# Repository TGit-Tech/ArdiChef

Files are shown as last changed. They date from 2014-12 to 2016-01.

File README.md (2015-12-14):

-----------------------------------------------------------------------------------
#ABOUT
-----------------------------------------------------------------------------------
ArdiChef is a project that will attempt to automate home cooking
and cleaning.  The project will utilize

    - Arduino microcontroller kits
    - 3D Printed food dispensing parts
    - Purchased pumps, motors and miscellaneous hardware

ArdiChef will take a factory automation approach in dealing with
food preparation much like a in-home food factory.

-----------------------------------------------------------------------------------
#Project Status
-----------------------------------------------------------------------------------
ArdiChef is still in a development phase and has no official releases.  

RELEASE TARGET-DATES

    * 1/2016    v1.0 - Basic ingredient dispensing (ArdiChef-100 Releasing Soon)
    * 6/2016    v2.0 - Ingredient mixing & prep
    * 1/2017    v3.0 - Cooking
    * 6/2017    v4.0 - Self Cleaning abilities

-----------------------------------------------------------------------------------
CONTRIBUTING
-----------------------------------------------------------------------------------
Anyone interested in joining this project can email
tgit28@gmail.com with a return email address.  Details of what can
be done and what needs done can be negotiated from there.

We'd really appreciate any extra man-power we can gather..

CONTRIBUTORS

    Thomas G.      Project Started         tgit28@gmail.com
    
-----------------------------------------------------------------------------------
WERE TO GO FROM HERE
-----------------------------------------------------------------------------------
ArdiChef has a website at http://www.ArdiChef.com that shows more
details on what has been made and how to assemble the items finished.

Also take a look at /documents/ArdiChef_v1.0.pdf for project details.
https://github.com/tgit23/ArdiChef/blob/master/documents/ArdiChef_v1.0.pdf

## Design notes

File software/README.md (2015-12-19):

# Software
#####For the ArdiChef Project
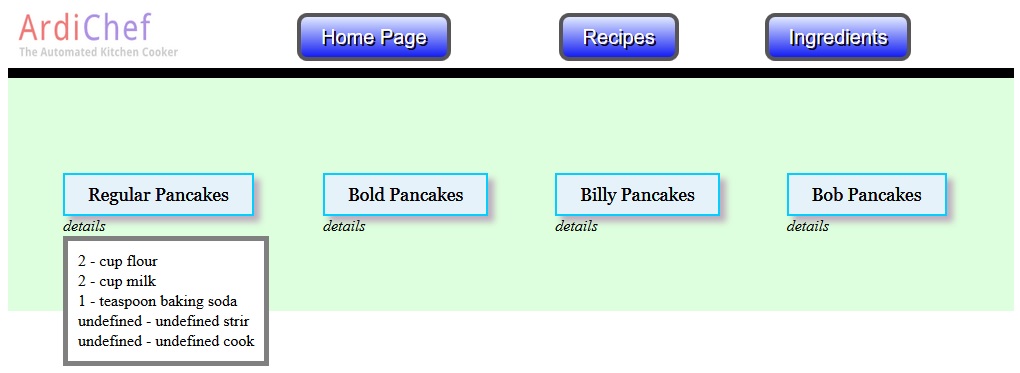
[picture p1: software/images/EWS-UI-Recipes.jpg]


-------------------------------------------------------------------------------------
##Choosing a Hardware Configuration
-------------------------------------------------------------------------------------
1. ArdiChef will support various hardware configurations to meet complexity needs
    - Single Arduino Board
    - Single Arduino Board with Ethernet Shield (*SUGGESTED*)
    - One Arduino Board and one Rasberry Pi
    - Multiple Arduino Boards with a "master" Arduino Board with an Ethernet Shield
    - Multiple Arduino Boards with one Rasberry Pi

-------------------------------------------------------------------------------------
##Software Installation ( Single Arduino with Ethernet )
-------------------------------------------------------------------------------------
1. Arduino Setup
    - Load ArdiChefController into Arduino Sketch
    - Set Pre-Compiler Directives
        - IP Adress
        - Gateway
        - Subnet
    - Compile and Upload to the Arduino
    
    - Setup the EWS
        - Copy all files within the EWS folder to the Ethernet Shield SD-Card
        - Plug the card back into the Ethernet Shield
        
-------------------------------------------------------------------------------------
##Architecture
-------------------------------------------------------------------------------------
- The main components of ArdiChef Software include
    - A **Storage** device
    - An Embedded Web Server (**EWS**) to host the files on the storage device
    - A Web **Browser** that supports Javascript for the User Interface
    - I2C or Serial **Communications** (*For Multiple Arduino Boards*)
    - **Ports** Dispatch/Pin routing and Various Motor/Heat/Other Driving objects (*Always on Arduino*)

- Single Arduino Board Configuration (*Still In Development*)
    - Storage = Recipe & Ingredient files reside locally on a USB attached home PC.
    - EWS = Files are hosted on the home PC
    - Browser = Any javascript enabled web browser on the home PC
    - Communications = USB -> |Firmata/Serial| -> Arduino
    - Ports = "ArdiChefController" Arduino Sketch

- Single Arduino Board with Ethernet Shield
    - Storage = Micro SD-Card
    - EWS = Arduino
    - Browser = Any Browser on the local network (ie. Home PC or Cell Phone)
    - Ports = "ArdiChefController" Arduino Sketch

- Single Arduino and Rasberry Pi (*Still In Development*)
    - Storage = Rasberry Pi
    - EWS = Rasberry Pi
    - Browser = Rasberry Pi (*Likely equiped with a touchscreen*) and/or Any Browser on the network
    - Ports = "ArdiChefController" Arduino Sketch

- Multiple Arduino Boards with a "Master" Arduino w/Ethernet (*Still In Development*)
    - Storage = Micro SD-Card on Ethernet Shield
    - EWS = "Master" Arduino Board
    - Browser = Home PC or Cell on the network
    - Ports = "ArdiChefController" Arduino Sketch loaded on every Arduino Board Used
    
-------------------------------------------------------------------------------------
#Folders
-------------------------------------------------------------------------------------
| Folder | Contents |
| --- | ---|
| /ArdiChefController | Main Control software for Arduino Board(s) |
| /EWS (Embedded Web Server) | The files that make up the web based user interface |
| /WebServerST_Plus | Arduino Sketch for the Arduino Ethernet shield enabling EWS hosting |

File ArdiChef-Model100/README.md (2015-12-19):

#Building the ArdiChef
### Model-100
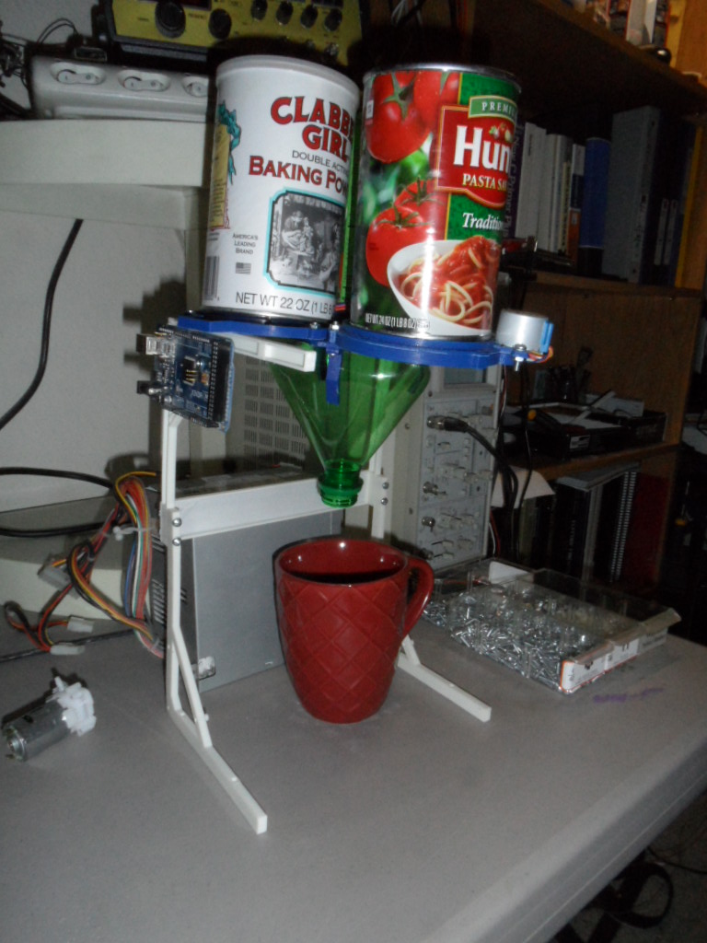
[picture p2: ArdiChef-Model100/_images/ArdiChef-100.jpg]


-------------------------------------------------------------------------------------
#Overview
-------------------------------------------------------------------------------------
- Features
    - (3) Dry Powder or Granular Ingredient Dispensing
    - Stand
        - Built from 3D Printed Parts
        - Dimensions: 11-1/4" Heigh x 8" Wide x 10-1/2"
        - 6-1/2" Nozzle Clearance
        - Mounting holes for Arduino Mega

- Example Uses
    - Simple Pancake batter w/o Eggs
    - Coffee Subliment dispensing

-------------------------------------------------------------------------------------
#Required Materials
-------------------------------------------------------------------------------------
- Household Items ~$7
    - (3) 86mm Diameter Tin Cans (ie. *Canisters*)
        - Example Items:
            - Hunts Pasta Sauce
            - Cambells Family Size Soup Cans
    - (1) 2-Liter Coca-Cola Brand Plastic Pop Bottle
        - Example Items:
            - 2-Liter Barq Root Beer
            - 2-Liter Sprite
            - 2-Liter Coca-Cola

- 3D Printed Items
    - (3) Food Dispensers (*ArdiChef Part ID: PD-FBD-28BYJ-86MM*)
    - (4) Stand Legs
    - (3) Funnel Brackets for 2-Liter pop bottle
    - Center Clamp
    - Stand Cross Member

- Electronic Hardware ~$44.10
    - Arduino AtMega 2560 Controller Board
        - <a href="http://www.gearbest.com/development-boards/pp_18651.html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" target="_blank">Arduino Mega $10.75</a>
    - Arduino Ethernet Shield with SD-Card support
        - <a href="http://www.banggood.com/Ethernet-Shield-W5100-Mega2560-R3-ATmega2560-16AU-Kit-For-Arduino-p-957681.html" target="_blank">Arduino Mega w/Ethernet Shield $17.00</a>
    - SD-Card with ability to transfer files
        - <a href="http://www.banggood.com/8GB-Class-10-Micro-SD-Card-TF-Card-With-Card-Adapter-For-Cellphone-p-1009135.html" target="_blank">8GB Class 10 Micro SD with Adapter $6.29</a>
    - Ethernet Cable
        - <a href="http://www.gearbest.com/cables-connectors/pp_68121.html" target="_blank">Retractable Ethernet Cable $1.40</a>
    - (3) 2BYJ-48 5Vdc Step Motor with ULN2003 driver board
        - <a href="http://www.gearbest.com/development-boards/pp_45177.html" target="_blank">28BYJ w/ULN2003 $3.47</a>
    - PC Power Supply
        - <a href="https://www.allhdd.com/power-supply/desktop-power-supply/250-watt/nps-250kb-f-dell-250-watt-power-supply-for-optiplex.-new-pull./" target="_blank">Dell 250W Power Supply Used $9</a>

- Mechanical Hardware
    - Machine Screws
    - Can Opener
    - Screw driver and Socket or Anything to hold the nut

-----------------------------------------------------------------------------------
##Assembly
-----------------------------------------------------------------------------------
1. Prepare (3) PD-FBD-28BYJ-83MM Food Dispensers
    - Build Instructions at: [../dispensers/PD-PowderDispensers/PD-FBD-28BYJ-86MM/README.md](../dispensers/PD-PowderDispensers/PD-FBD-28BYJ-86MM/README.md)
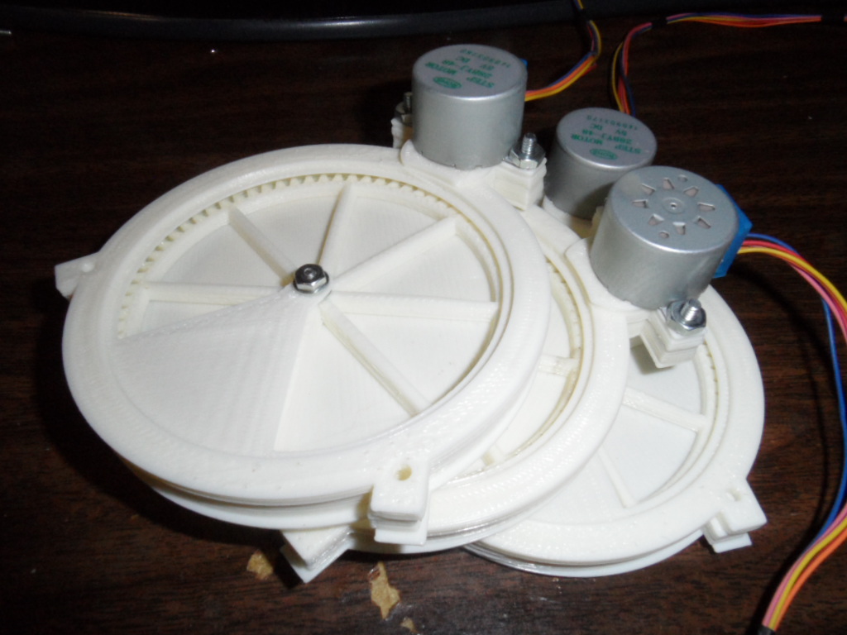
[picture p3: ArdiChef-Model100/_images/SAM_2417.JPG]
    
    
2. Attach the Dispensers together into a Triangular Collection
    - Insert #4 Machine Screws upwards in all three dispensor's side fastener holes
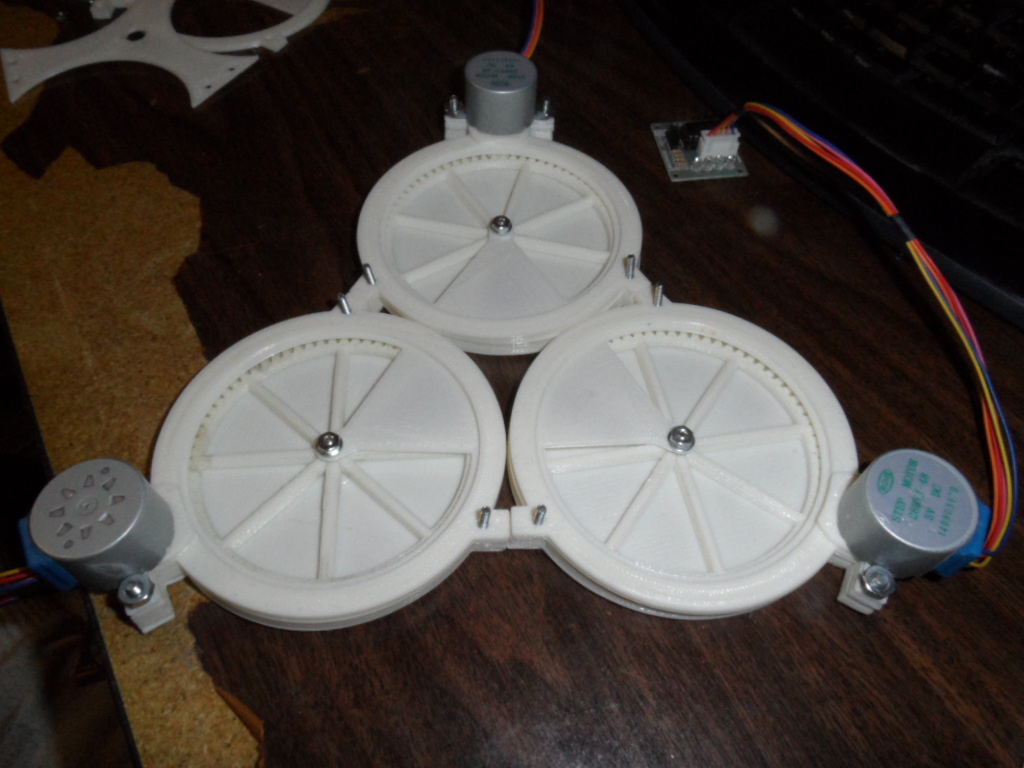
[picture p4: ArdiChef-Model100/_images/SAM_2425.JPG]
    
    - Using a can opener remove both ends of the selected cans
    - Place the cans on top of the (3) dispensers
    - Place the "Center Clamp" in the center of all 3-canisters
    
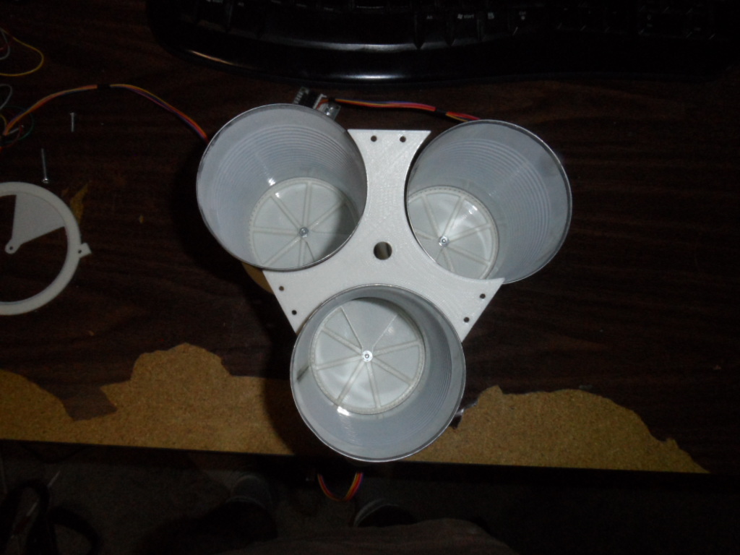
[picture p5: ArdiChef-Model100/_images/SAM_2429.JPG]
    
    - Tighten the "Center Clamp" using (6) #4 Nuts
    
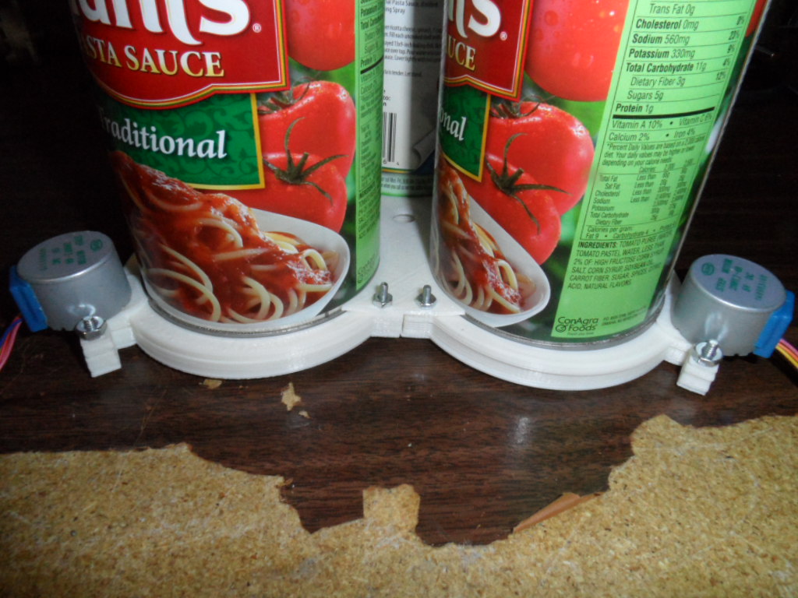
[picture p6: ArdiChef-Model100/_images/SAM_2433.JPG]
    
    - Note: *Sometimes its easier to bolt in one can at a time as long as the result is the same*
    
3. Attach the Stand
    - Using two adjacent motor bolt holes attach the stand legs to the dispenser collection
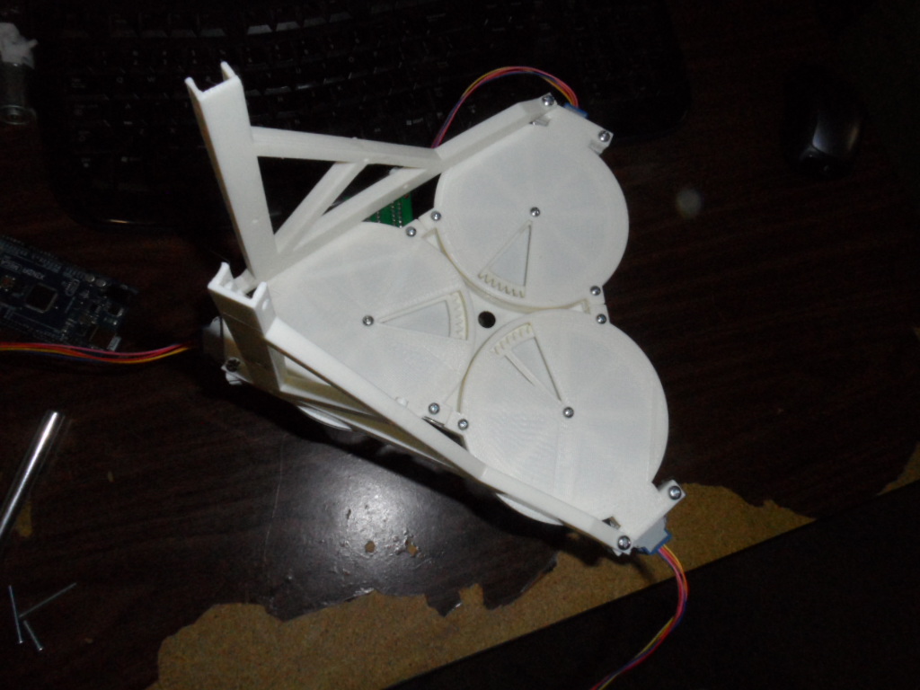
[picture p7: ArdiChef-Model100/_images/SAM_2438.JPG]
    
    
3. Attach the 2-Liter bottle as a hopper
    - Cut the 2-Liter bottle in half where the top part of it's label is
    -

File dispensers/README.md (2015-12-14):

# Food Dispensers for the ArdiChef Project
-------------------------------------------------------------------
#Labelling
-------------------------------------------------------------------
- Food Dispensers are labelled using the form 'Type'-'Model'-'Motor'-'MaxSize'-'Revision'
    - Types
        - PD = Suitable for Powder Foods Dispensing
        - GD = Suitable for Granular Foods Dispensing
    - Model
        - FBD = Full Bottom Drop
        - TDS = Top Down Scrape
    
    - Motor = Stepper Motor Model#
    - MaxSize = The largest Canister Diameter for this design
    - Revision = Optionally supply a Revision of the design

-------------------------------------------------------------------
#Examples
-------------------------------------------------------------------
- Part: PD-FBD-28BYJ-86MM
    - Powder Food Dispenser
    - Full Bottom Drop Model
    - Using 28BYJ Step Motor
    - Model Fits up to a 86mm Maximum Canister Diameter
    - No Revision version supplied

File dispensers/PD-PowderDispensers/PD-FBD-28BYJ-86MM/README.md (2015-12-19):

# Assembly Instructions
### For Part: PD-FBD-28BYJ-86MM
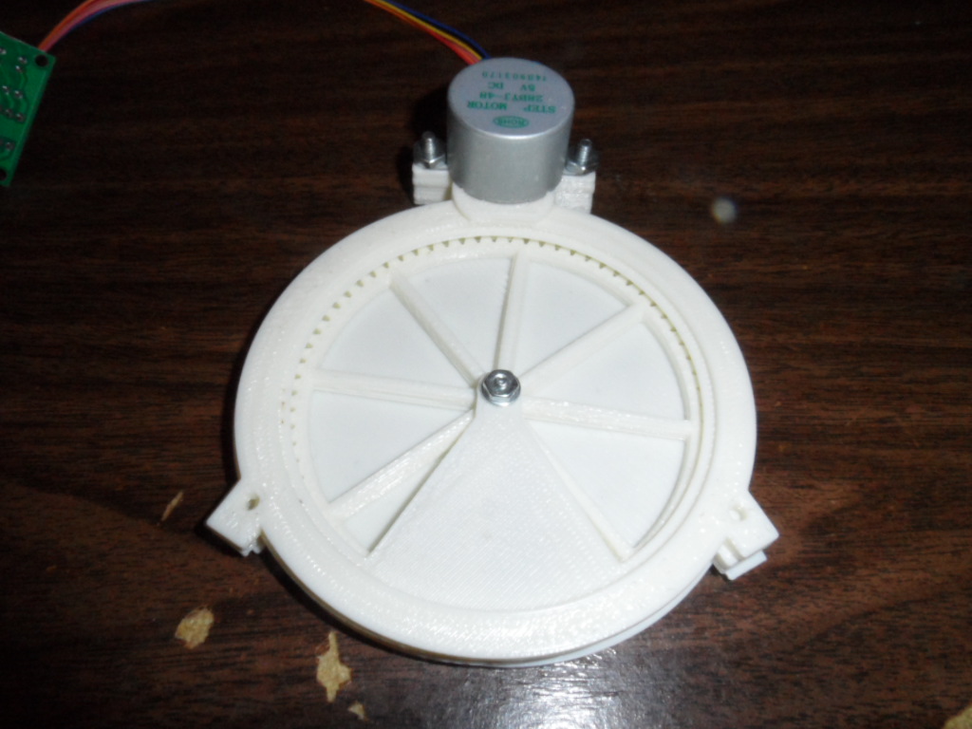
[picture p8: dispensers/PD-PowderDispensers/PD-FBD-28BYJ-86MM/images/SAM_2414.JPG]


-----------------------------------------------------------------------------------
## Bill Of Materials
-----------------------------------------------------------------------------------
1. 3D Printed Parts
    - Canister Cover
    
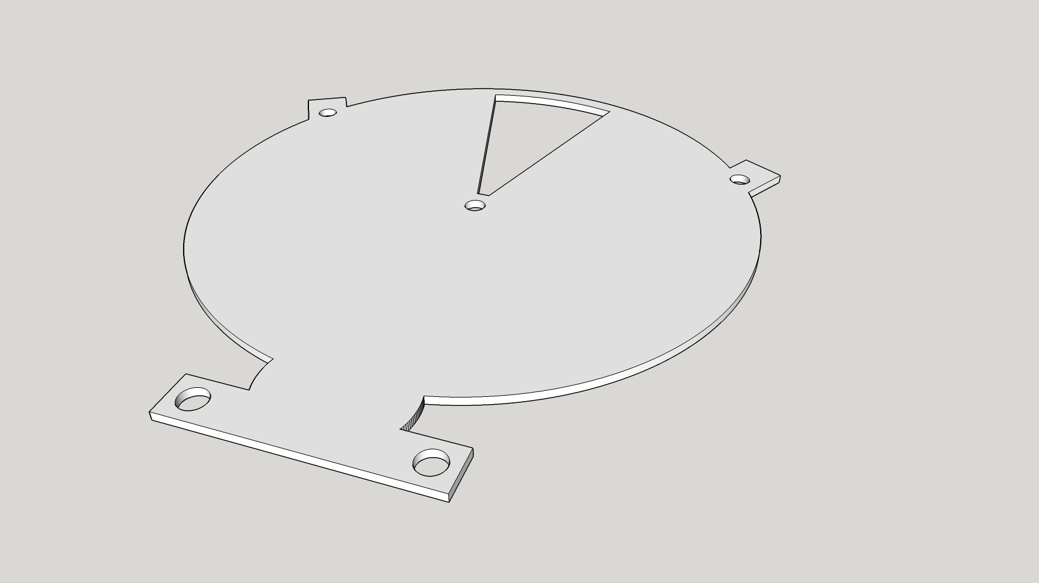
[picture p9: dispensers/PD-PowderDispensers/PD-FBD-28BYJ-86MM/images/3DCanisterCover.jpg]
    
    - Center Ring
    
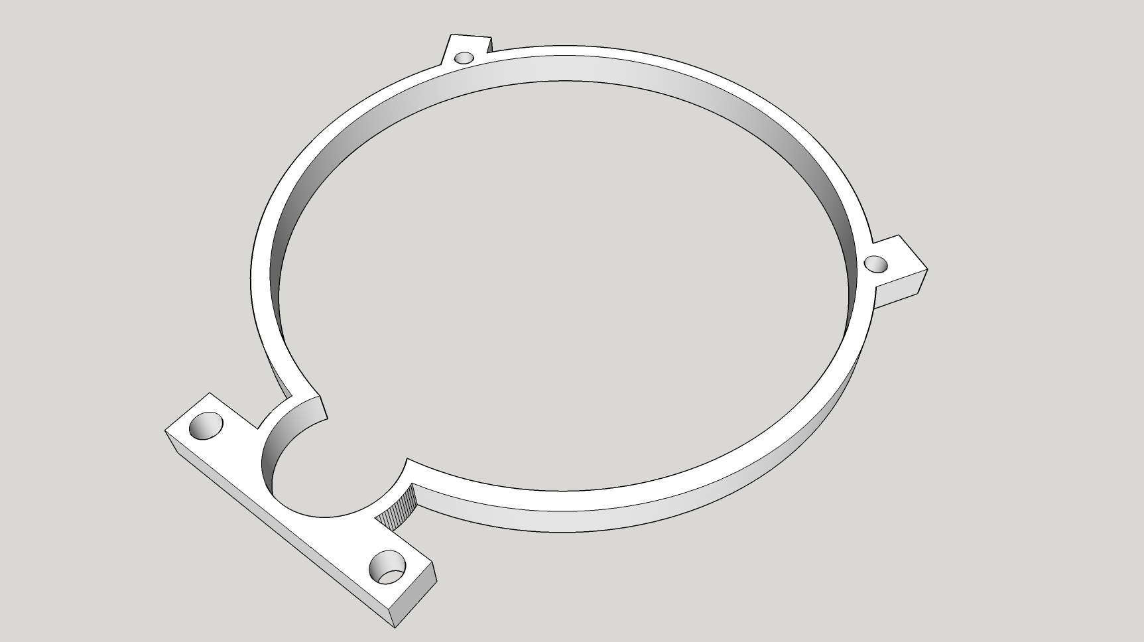
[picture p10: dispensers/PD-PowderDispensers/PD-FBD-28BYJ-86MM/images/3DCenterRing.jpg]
    
    - Dispense Gear
    
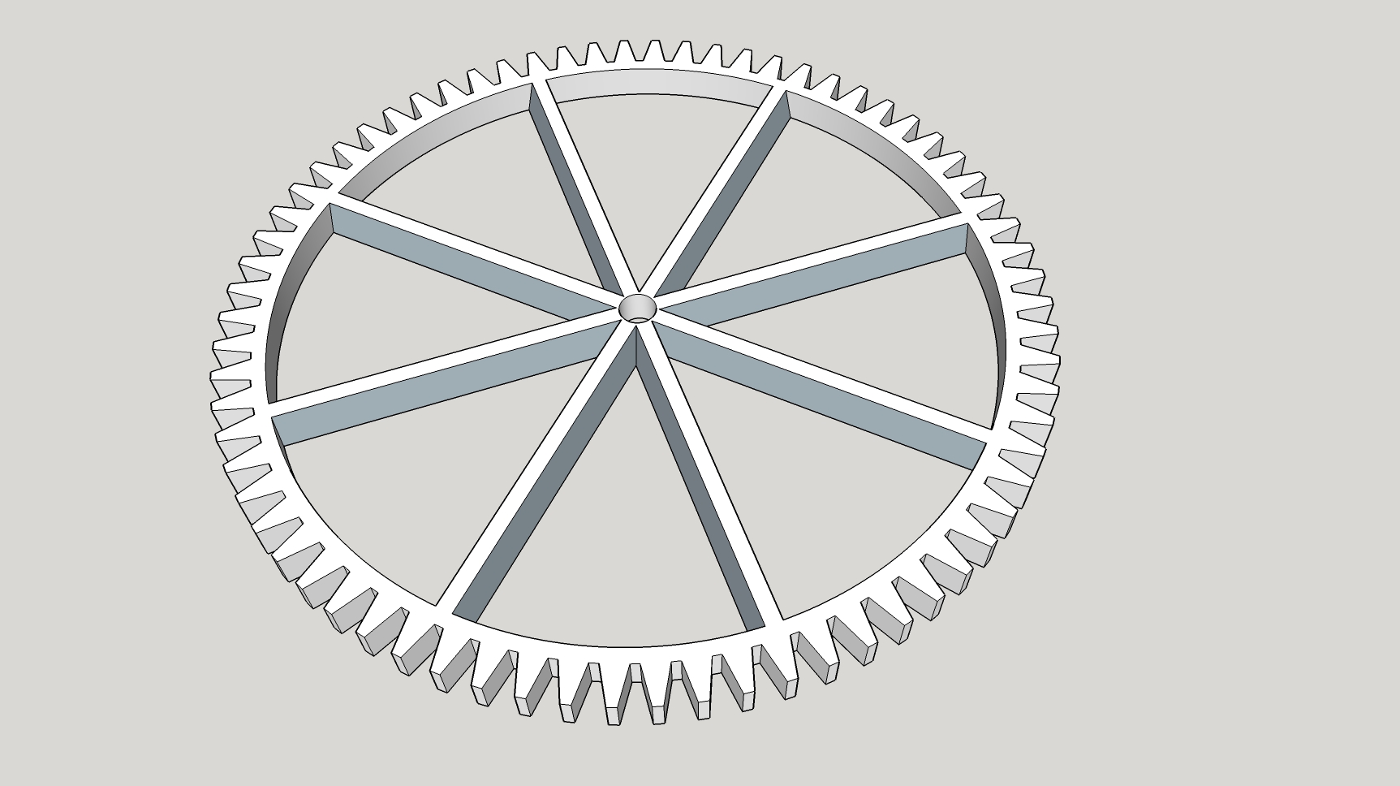
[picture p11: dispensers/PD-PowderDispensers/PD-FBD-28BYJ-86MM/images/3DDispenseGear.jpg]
    
    - Motor Gear
    
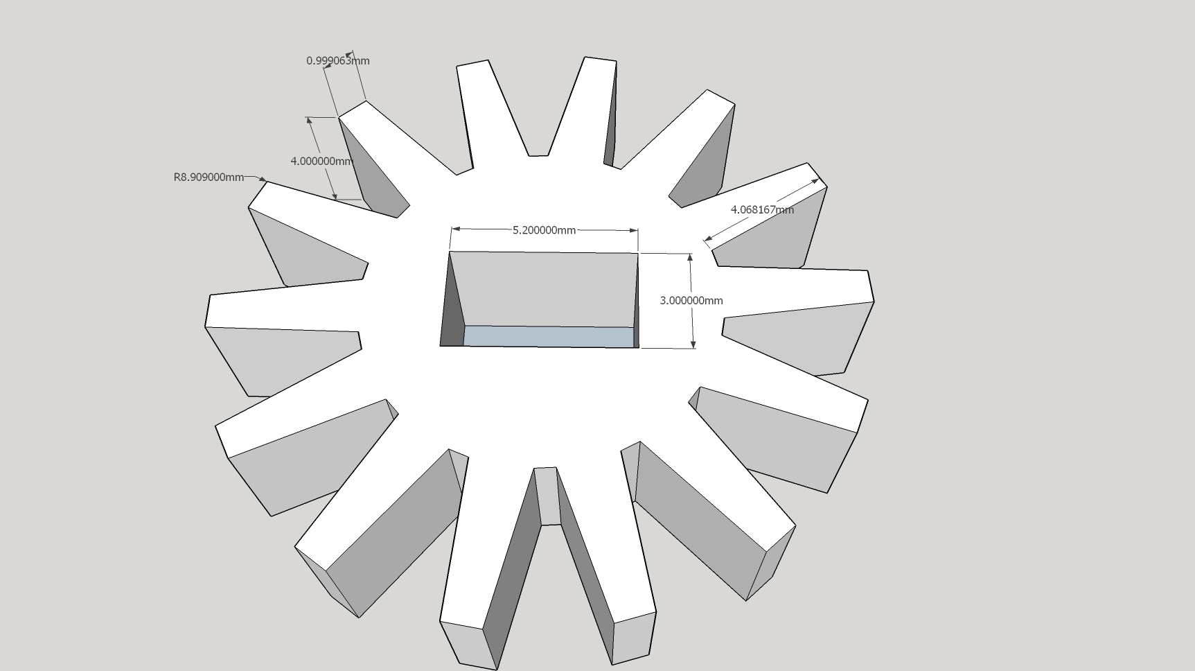
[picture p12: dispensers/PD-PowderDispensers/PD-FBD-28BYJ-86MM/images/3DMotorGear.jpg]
    
    - Canister Base
    
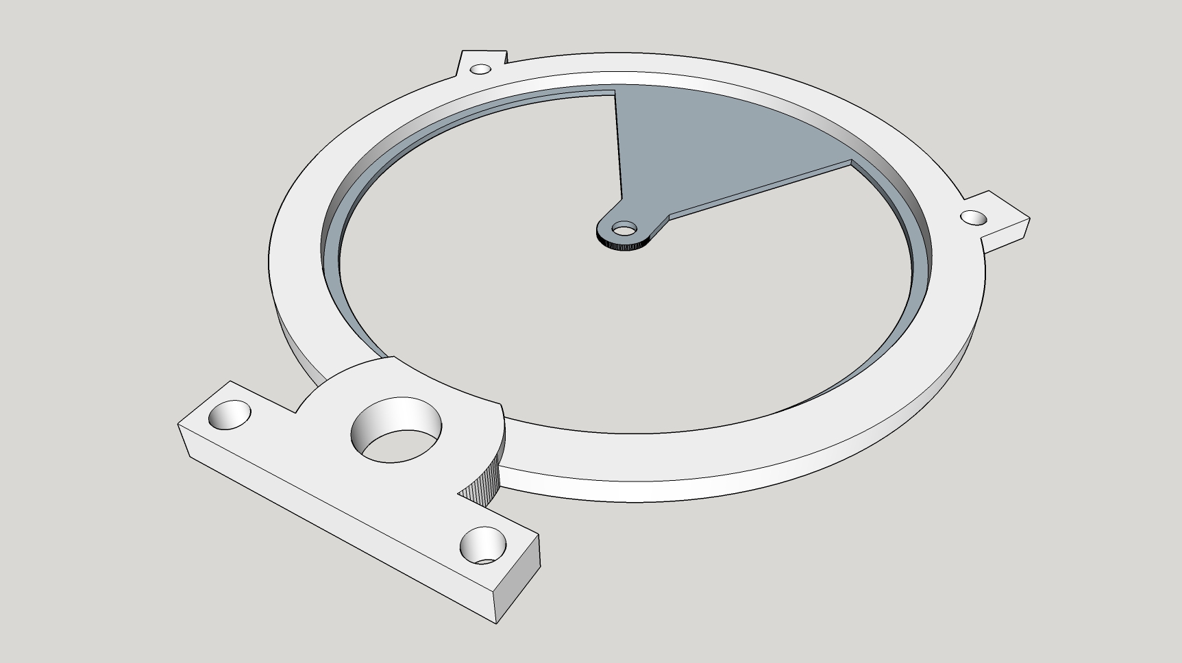
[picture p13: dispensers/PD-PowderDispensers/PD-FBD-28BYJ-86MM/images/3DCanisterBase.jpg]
    
    
2. Hardware
    - (3) #4 x 3/4" Machine Screws
    - (3) #4 Nuts
    - (3) #4 Flat Washers
    - (2) #6 or #8 x 3/4" Machine Screws
    - (2) #6 or #8 Nuts
    
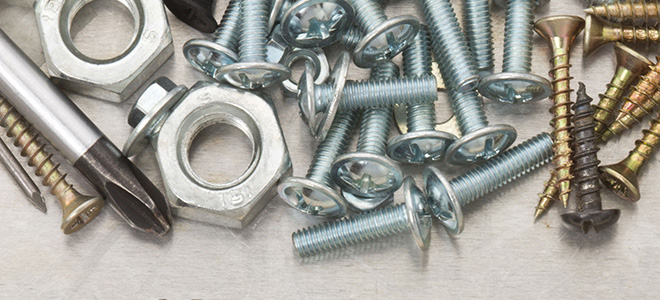
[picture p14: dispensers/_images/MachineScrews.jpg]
    
    - 28BYJ-48 Step Motor
    - ULN2003 Step Motor Driver Board
    
    
        
-----------------------------------------------------------------------------------
## Assembly
-----------------------------------------------------------------------------------
1. Place the "Canister Cover" on Work bench (smooth side up)
    - Insert a #4 x 1/2" Bolt upwards through the center
    - Place a #4 flat washer on the bolt
    - Place the "Center Ring" on top of the "Canister Cover"
    
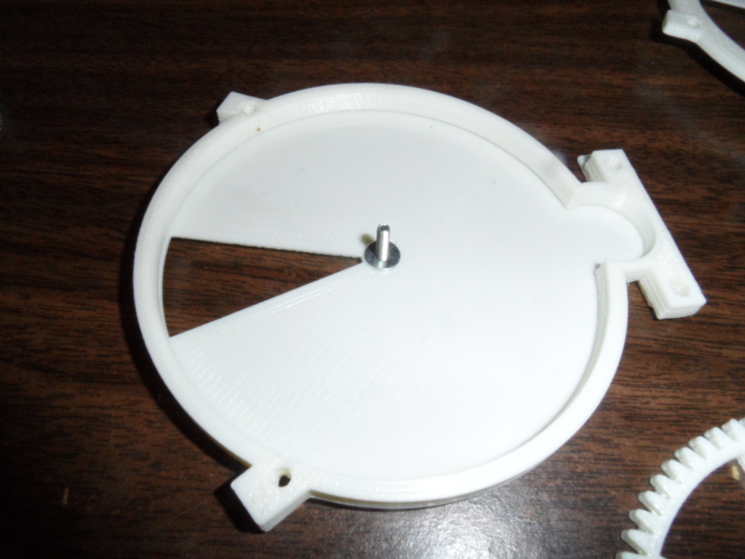
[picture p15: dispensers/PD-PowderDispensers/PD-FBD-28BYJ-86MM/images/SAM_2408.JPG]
    
    
3. Place the "Dispense Gear" inside the "Center Ring"
    - Place 2 - #4 Flat Washers on top
    
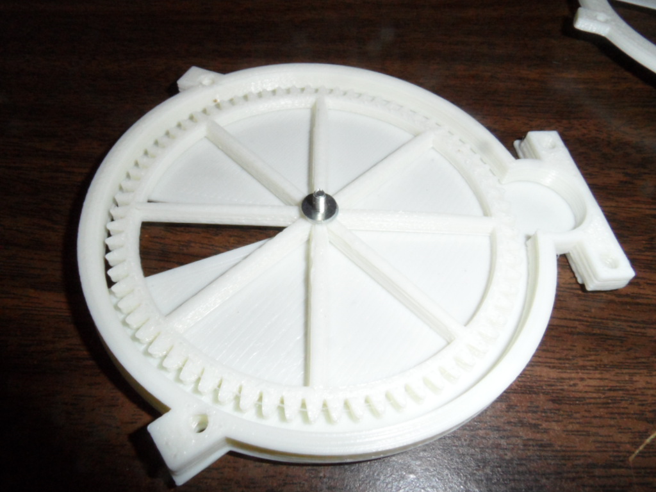
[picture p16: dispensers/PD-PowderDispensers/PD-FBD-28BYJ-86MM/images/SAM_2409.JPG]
    
    
4. Place Stepper Motor under the Canister Base (Motor meshes with the coarse side - Smooth surface up)
    - Attach the "Motor Gear" to the motor shaft (Smooth surface up)
    
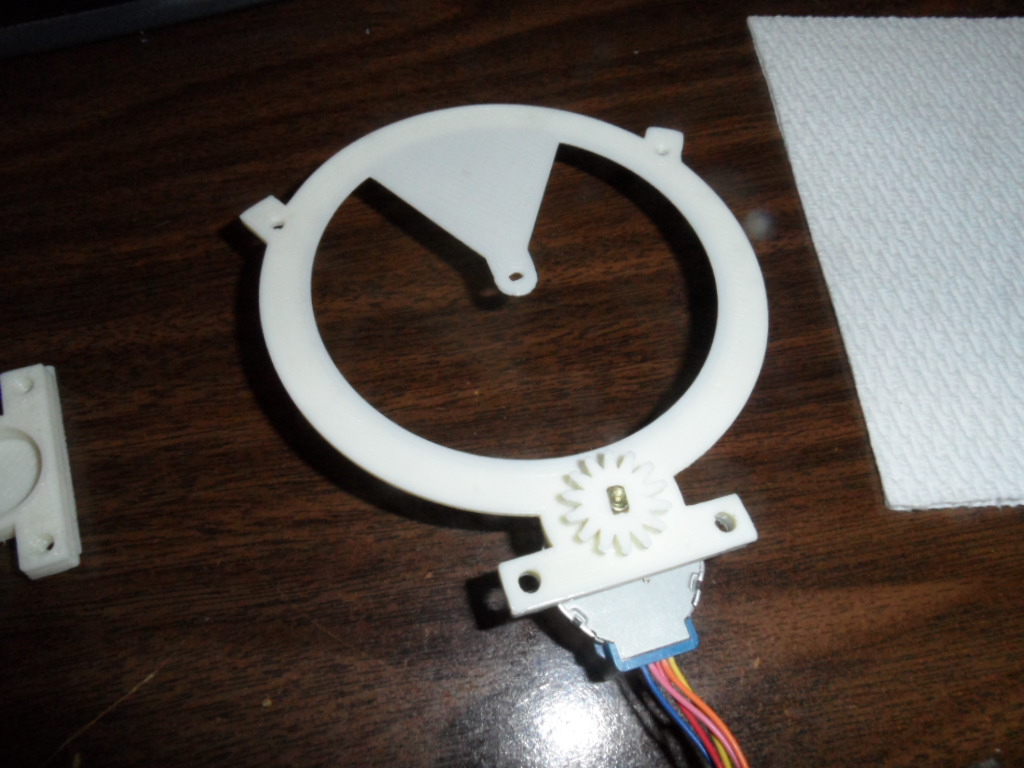
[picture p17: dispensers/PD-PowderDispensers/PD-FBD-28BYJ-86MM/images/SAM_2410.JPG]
    
    
5. Flip the "Canister Base" with Motor and place on top of the "Center Ring"
    - Attach a #4 Flat Washer on top
    
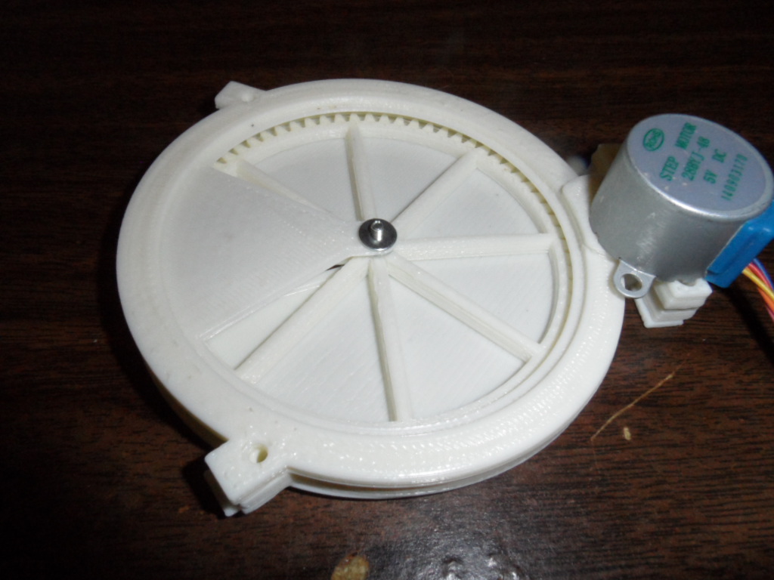
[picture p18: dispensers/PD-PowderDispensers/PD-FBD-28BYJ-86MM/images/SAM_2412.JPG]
    
    
6. Fasten the motor to the despenser
    - Use #6 x 3/4" Machine Screws
    


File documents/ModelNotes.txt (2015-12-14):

1) If "model repair service" (https://netfabb.azurewebsites.net/) keeps filling in a hole in the model
    The outer shell needs to be erased by creating the two planes (say 2mm above each other)
    Intersect face with center nut on both - fill in edges
    erase the outer edge from underneath
    
2)

------------------------------------------------------------------------------------------------------
Drawing Gears in Skethup (NONE OF THESE TRICKS WORK!!)
------------------------------------------------------------------------------------------------------
Gears in the ArdiChef Project use the attached worksheet to calculate circle radius and sides.

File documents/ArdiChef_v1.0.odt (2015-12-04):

ArdiChef Project

The Automated Kitchen Cooker

Started By: Thomas G (12/2014)

Feel free to use: no strings attached (text content only / images respectfully referenced)

# INTRODUCTION

The ArdiChef project will reside within http://www.github.com/tgit23/ArdiChef/

## Software

The software will mostly be written using the Arduino programming software package along with the "Processing" programming language.

## Control

The ArdiChef project will be controlled using the Arduino project (http://www.arduino.cc/) micro-controller board and mimic a lot of the 3D RepRap printer project technologies.

## Hardware

- Repository of Models - http://www.github.com/tgit23/Ardichef/ → Hardware/
- Bill of Materials

Many of the hardware parts are printed using a 3D printer while some will need to be purchased. Currently all 3D printed parts are designed in Google Sketchup and stored at

# FOOD DISPENSERS

## Granular Foods Dispenser (GFD-28BYJ)

Granular foods like sugars and spices can be dispensed using what I'd call the Gumball approach. A circular plate with holes in it rotating to a covered drop-hole.

### 1-Gallon Can Granular Foods Dispenser (GC-GFD-28BYJ)

The 1-Gallon granular food dispenser requires

- One Gallon Tin Can with a base diameter that measures 16.125 inches
- 28BYJ-48 5Vdc 4-Phase 5-Line Stepper Motor with ULN2003 Driver Module Board
- 3D Printer for printing the following parts @ http://www.github.com/tgit23/ArdiChef → /Hardware/GranularDispensers

File-Name | Google Sketchup | Thumb | Description
MotorMount.skp | 2014 - Inches | | 1) The 28BYJ Stepper motor is bolted into this motor mount (Shaft up)
DispGear_4inHoles.skp | 2014 -Inches | | 2) The Disp (Dispense) gear is placed on the motor shaft
GallonCanBase_6pt125inchBase.skp | 2014 - Inches | | 3) The “MotorMount/Stepper/DispGear” assembly is then bolted to the CanBase 4) The Assembly is then attached to the bottom of the One-Gallon tin can.
MotorMountSpout.skp | 2014 - Inches | | 5) Optionally – A spout holder can be attached to the MotorMount under the dispensing hole.

## Powder Foods Dispenser (PFD-28BYJ)

### 1-Gallon Can Powder Foods Dispenser (GC-PFD-28BYJ)

The 1-Gallon powder food dispenser requires

- One Gallon Tin Can with a base diameter that measures 16.125 inches
- 28BYJ-48 5Vdc 4-Phase 5-Line Stepper Motor with ULN2003 Driver Module Board
- 3/4” Shedule 80 PVC Pipe threaded and notched the height of the tin can
- 3/4” PVC Pipe Nut (Created by cutting a PVC cap)
- 3D Printer for printing the following parts located at http://www.github.com/tgit23/ArdiChef/ → Hardware/PowderDispensers/GallonCan_ThreeQtrPipe

File-Name | Build Instructions

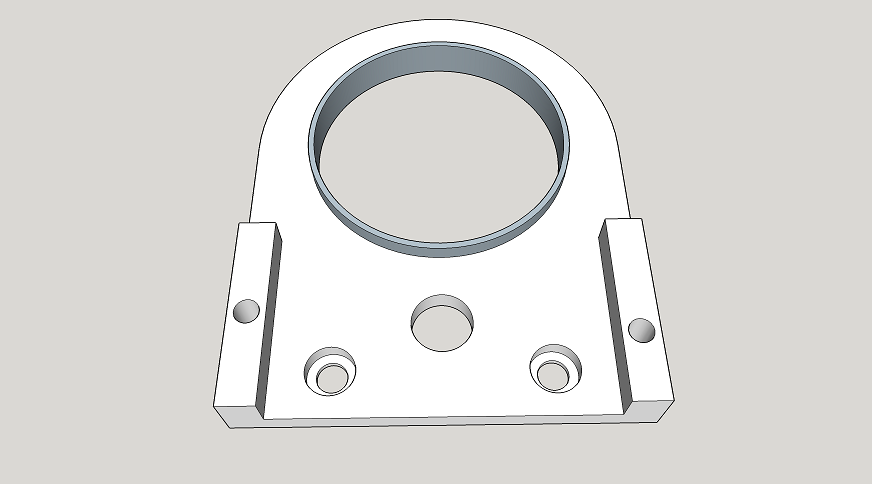
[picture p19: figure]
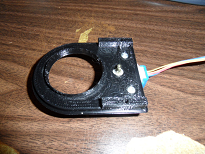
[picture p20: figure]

MotorMountGearBox.skp | 1) The 28BYJ Stepper motor is bolted into this motor mount gear box (Shaft up)
MotorGear.skp | 2) The MotorGear is placed on the motor shaft

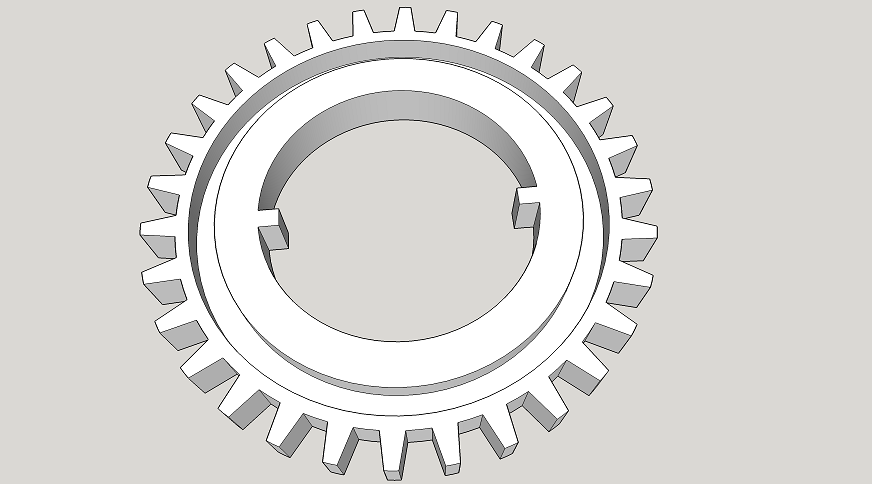
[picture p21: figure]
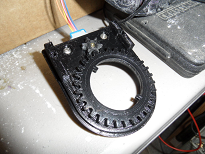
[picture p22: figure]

PipeDriverGear_24D.skp | 3) The PipeDriverGear is dropped freely into the MotorMountGearBox.

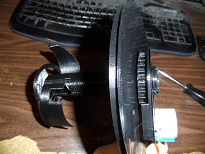
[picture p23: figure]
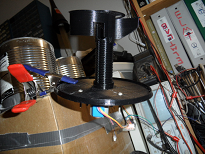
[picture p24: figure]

DispenserPipe_24D_Complete.skp CanBase_24D_1Thread.skp | 4) The MotorMountGearBox with PipeDriverGear and MotorGear Assembly is then bolted to the bottom of the CanBase. 5) The Dispensor is then Threaded Through the CanBase

### Cambells 26.25Oz Family Size Can Powder Foods Dispenser (CC-PFD-28BYJ)

The Family Size Cambells Soup Can powder food dispenser requires

- One Family Size Cambells Soup Can with a base diameter that measures 3 3/8 inches
- 28BYJ-48 5Vdc 4-Phase 5-Line Stepper Motor with ULN2003 Driver Module Board
- 1/2” Shedule 80 PVC Pipe threaded and notched the height of the tin can
- 1/2” PVC Pipe Nut (Created by cutting a PVC cap)
- 3D Printer for printing the following parts located at http://www.github.com/tgit23/ArdiChef/ → Hardware/PowderDispensers/Cambells_26.26OZ_HalfInchPipe

File-Name | Google Sketchup | Thumb | Build Instructions
MotorMountGearBox.skp | 2014 - Inches | | 1) The 28BYJ Stepper motor is bolted into this motor mount gear box (Shaft up)
MotorGear.skp | 2014 -Inches | | 2) The MotorGear is placed on the motor shaft from /PowderDispensers/GallonCan_ThreeQtrPipe
PipeDriverGear.skp | 2014 - Inches | | 3) The PipeDriverGear is dropped freely into the MotorMountGearBox.
Scrapper.skp | 2014 - Inches | | 4) A 1/2” Schedule 80 PVC pipe is threaded the height of the gallon can in use 5) Using a dremel with grinder stone create 2-notches vertically along the pipe for the DriverGear 6) The Scrapper is attached (glued) to the top of the 1/2” Threaded and notched PVC pipe.
CanBase_Campbells26.25OZ.skp | | | 7) A PVC Nut (A cut in half PVC Cap) is glued into the CanBase 8) The CanBase is then attached to the bottom of a one-gallon tin can 9) The “MotorMountGearBox/MotorGear/PipeDriverGear” assembly is bolted to the CanBase. 10) The Threaded and Notched “PVC-Pipe/Scrapper” is threaded down the CanBase Nut till the PipeDriverGear's Notches catches the Notches in the PVC pipe.

# SOFTWARE

## Architecture

SD-Card ------------------------------------------------------------------ Recipes.json Webpages.htm | Ingredients.json | I2C.json Interface Device ----------------------------- PC Tablet / Cell Phone Rasberry Pi Arduino-#0 or Rasberry Pi ------------------------------------------ WebServerST <-- |--> Master Engine ==================================== Depending on configuration Arduino #0 can host or Rasberry Pi Firmata Ethernet Motors Arduino #4 ------------------------------------------ I2C ========================== Motor Drivers Arduino ------------------ I2C =========== Motor Drivers If the Server is hosted on arduino The runtime.json is used to buffer Commands ELSE an I2C in/out Buffer on the Rasberry Pi is used.

- Hardware
  - Interface Device = Any device with a web browser
  - Arduino's = A master Arduino(#0) and any other Arduino's numbered according to their I2C address
  - Storage = SD-Card connected to Arduino #0
- Software
  - WebServerST = Renders html pages on the SD-Card, Parses AJAJ request that trigger the Master Engine
  - Master Engine = Processes requests; using Recipe.json & Ingredient.json data and outputs to → runtime.json
  - I2C communications
    - On Arduino #0 = Transmits action commands on the I2C communication bus
    - Other Arduino's = Recieves action commands
  - Drivers = Transforms “action commands” into motor activation

## Files

- Web-Pages
  - index.htm = Section (Buttons “ingredients”, “recipes”, and “manual”); Section (Buttons for all “favorite” recipes)
  - ingredients.htm = HMI type display with ingredients JSON and entries/buttons for Ingredients.json file editing
  - recipes.htm = Load, Edit, Add and Execute (IE. Send to Engine); various recipes files

### Index (json/htm)

- Top Section will have 3-Buttons to access other htm pages; “Recipes”, “Ingredients”, and “Manual” (i.e. for manual control)
- Bottom Scroll-able Section will have dynamic instantly run recipe buttons part of a category known as “favorite” recipes
  - Favorite recipe names will be stored in index.json and have a “Remove” and “Portion Size” button/fields.

### Ingredients (json/htm)

#### Ingredients.htm

- HMI graphical view of Canisters, Cooking and stuff that make up the ArdiChef.
  - Canisters should graphically show their current product level and at the top show their total capacity.
  - Each information field should be editable by clicking on it
  - Also include an “Add” button to add new Ingredient/Operation

FLOUR SUGAR

------------- ======

------------- ======

motor motor

driver driver

pulze-oz pulse-oz

manual pin manual pin

#### Ingredients.json

  - Top object ID = Arduino # (IE. 0 for master or I2C address #)
  - Digital Pins = The digital pins used by a dispenser/operation (e.g. 1-4 or 1,5,8 or etc...)
  - Ingredient = A text name for product or operation
  - Driver = The driver module name to use for motor activation; Different drivers will require more/dynamic settings
    - 28BYJ

### Recipes (json/htm)

- Recipes.htm
  - Loads recipes.json behind the scenes (AJAJ) and display as many recipe-blocks as possible; Each block having
    - Name = Recipe Name
    - “Portion” = Serving Size
    - “Edit” = Open 'this' recipe in “Recipe.htm” for editing and/or removal
    - “Favorite” = Add Recipe name to 'index.json' to display it on the home page
  - “Add” button to allow adding new recipes
  - Recipes.htm will contain javascript to organize, sort, and find recipes
- Recipes.json - All JSON Recipes will initially be one file (may break apart later as project matures)
    - “Run” button – to execute the recipe
    - “Portion” field – to proportionate the recipe
    - “Favorite” button – to add the recipe to “favorites” on the home page
    - “Edit” button – to load a new 'htm' page that will
- RecipeEdit
  - May be implemented as a pop-over screen on the same web-page (this would be the ideal way to handle it, I think.)

## Implementation

- WebServerST
  - Must contain the ability to:
    - Serve GET files - for HTML page requests
    - Serve AJAJ files - for AJAJ page data
    - POST - Ability to trigger events(ie. functions) on the Master Engine
- Master Engine
  - Steps
    - Stream through recipes.json and find the recipe to operate on
    - Calculate the portion size
    - Stream through ingredients.json to decode the recipe to driver signals (recipe → I2C.json)
    - Build the I2C.json (i.e. driver messages) file and save it in the /I2Cstack so drivers can pick it up and execute
- I2C
  - I2C will communicate to Motor Driving Code in the form of “<PinsCSV>:Driver:Steps<\n>”
    - Thus each command will identify the motor pins, # of steps, and Driver board
- Drivers
  - Reads in commands from the I2Cstack and executes them (i.e. produces motor signals)

## Future Plans

- ArdiChef.com itegration
  - Add ability send current inventory and suggest recipes to/fro Ardichef.com
  - Add ability to share your recipes with everyone
    - Perhaps tap into an existing: food.com, myfridgefood.com, and etc...?
  - Web Server
    - Arduino -or- Rasberry Pi 2 Model B will be utilized as the Web-Host Server
    - The host will store
      - Recipes XML = Organize at least 3-hierarchy levels to contain a cooking reciepe
      - Hardware Setup XML = Which pins are connected to which dispensor models and ingredient contained there-in
      - Track Amount of Ingredients XML = Amount left inside the canister??? (May skip this for now)
    - Host Pages
      - Recipe (An “add”/”run” button on recipe browser)
        - Category - Breads
        - Name - Pancakes
        - Attribute - Blueberry (May be nice for fine adjustment or personality adjustments: Like: Drink->Coffee->MyName)
          - Ingredient Amount (Cup, Oz, Lb, etc...)
          - Ingredient Name (Flour, Sugar, etc..)
  - Web browser
    - The web browser will allow
      - Ability to upload recipes

# Up For Discussion

1. 4- Canisters into one spout or 4-spouts together
2. Turn-table or Conveyor Belt
  1. Turn-Table = Rotate bowl on circular table or rotate ingredients on circular table
  2. Conveyor Belt = Use bicycle tube as a food conveyor belt from start of ingredient canister row to an end drop position
3. Mixer on mixing bowl or over-head?

# Bill Of Materials (BOM)

## Tools

- 3D Printer

## Materials

## Original Purchases

Qty/SKU/Price | Product Name / Description | Picture

(2)

106842801

$30.54

www.gearbest.com

GZGW09 3D Printer Reprap Stepper Motor Driver Module Works with Official Arduino (http://www.gearbest.com/development-boards/pp_101725.html)

GZGW09 3D Printer Reprap Stepper Motor Driver Module

Step angle: 1.8 degree
Rated voltage: DC 4.83V
Rated current: 0.84A
Phase impedance: 5.75 Ohm + / - 10 degree centigrade
Phase inductance: 9.3 mH + / - 20 degree centigrade (1kHz 1V RMA)

Holding torque: 0.48 Nm
Shaft diameter: 5mm / 0.188
Shaft length: 20mm
Motor height: 34mm
Number of lead wire: 4 wires

Product Weight: 0.22 kg
Package Weight: 0.23 kg
Product Size(L x W x H): 5.8 x 4.2 x 4.2 cm / 2.28 x 1.65 x 1.65 inches
Package Size(L x W x H): 8.0 x 6.0 x 5.0 cm

http://www.gearbest.com/development-boards/pp_101725.html

http://www.dx.com/p/gzgw09-3d-printer-4-wire-stepper-motor-silver-black-222200#.Vk0qpuKaUQk


(3) NZ0019501 $11.22 www.gearbest.com | 28BYJ-48 5V 4-Phase 5-Line Stepper Motor with ULN2003 Driver Module Board (http://www.gearbest.com/development-boards/pp_45177.html) Google Sketchup 3" x 5 3/16" Rectangular Drive Hole
(2) NZ0049801 $75.24 www.gearbest.com | Arduino MEGA2560 RepRap Circuit Sets for 3D Printer Ramps (http://www.gearbest.com/development-boards/pp_64758.html) Package Contents: 1 x MEGA2560 Circuit Sets 1 x Ramps 1.4 4 x A4988 1 x USB Cable


(1) 277147 (http://www.dx.com/p/277147) $4.99 www.dx.com | Double Tip 21cm Dupont Cable - Black + Multicolored (70 PCS) (http://www.dx.com/p/277147) | (http://www.dx.com/p/277147)


(1) 145357 (http://www.dx.com/p/145357) $7.91 www.dx.com | 3-Pin Power Adapter Socket with Rock Switch for DIY Project - Black + Red (5-Piece Pack) (http://www.dx.com/p/145357) | (http://www.dx.com/p/145357)


(1) 344826 (http://www.dx.com/p/344826) $4.80 www.dx.com | S401 1/4" Water Flow Sensor for Dispenser / Coffee Machine - White (http://www.dx.com/p/344826) | (http://www.dx.com/p/344826)


(1) 263660 (http://www.dx.com/p/263660) $10.99 www.dx.com | DIY Copper Breadboard DuPont Connection / Test Cables - Multicolored (200 PCS) (http://www.dx.com/p/263660) | (http://www.dx.com/p/263660)


(1) 123648 (http://www.dx.com/p/123648) $1.46 www.dx.com | 2.54mm Mini Jumper Connector - Black (50-Piece Pack) (http://www.dx.com/p/123648) | (http://www.dx.com/p/123648)


(1) 162180 (http://www.dx.com/p/162180) $3.91 www.dx.com | 1-Pin Female to Female DuPont Cables for Arduino (2 x 40 PCS / 21cm) (http://www.dx.com/p/162180) | (http://www.dx.com/p/162180)
(1) 206265 (http://www.dx.com/p/206265) $1.77 www.dx.com | SZF303 Small Water Pump Motor Water / Oxygen Pipe / Tube - Transparent (100cm) (http://www.dx.com/p/206265) Model SZF303 Quantity 1 Color Transparent Material Plastic housing Features Use for small fish tank oxygen supply; DIY project Specification Inner diameter: 0.2cm; Thickness: 0.4cm; Length: 100cm Application Small water pump pipe / tube English Manual/Spec No Packing List 1 x Water pipe Dimensions: 39.37 in x 0.16 in x 0.16 in (100.0 cm x 0.4 cm x 0.4 cm) Weight: 0.32 oz (9 g) | (http://www.dx.com/p/206265)


(1) 232242 (http://www.dx.com/p/232242) $2.41 www.dx.com | DIY Plastic Water Pump Line Tube - White (4 PCS) (http://www.dx.com/p/232242) Brand N/A Quantity 4 Piece(s)/pack Color White Material Plastic Compatible Models Small water pump Application Used to connect small water pump Other Feature Outer diameter: 4mm; Inner diameter: 3mm Packing List 4 x Water pump line tubes Dimensions: 1.14 in x 0.71 in x 0.16 in (2.9 cm x 1.8 cm x 0.4 cm) Weight: 0.18 oz (5 g)


(1) 203330 (http://www.dx.com/p/203330) $4.99 www.dx.com | 20904 Silicone Tube Pipe - Translucent White (5 Meters) (http://www.dx.com/p/203330) Model 20904 Quantity 1 Color Translucent white Material Silicone Specification Outer diameter: 5mm; Inner diameter: 3mm; Thickness: 12mm; Working temperature range: -65'C~200'C Features Silicone tube Application Widely used for water dispenser, coffeemaker, electronic instrument, medical equipment, wine connection tube etc. English Manual/Spec No Packing List 1 x Silicone tube (5 meters) Dimensions: 196.85 in x 0.20 in x 0.20 in (500.0 cm x 0.5 cm x 0.5 cm) Weight: 2.82 oz (80 g) | (http://www.dx.com/p/203330)


(2) 236808 (http://www.dx.com/p/236808) $5.23 www.dx.com | HSYY01 Micro Gear Water Pump Motor w/ Hose - White + Silver (http://www.dx.com/p/236808) $5.23 Brand N/A Model HSYY01 Quantity 1 Color White + Silver Material Iron casing + PVC Specification Working voltage: 4~12V; Working current: 0.8A; Motor diameter: 2.7cm; inlet opening outer diameter: 0.4cm Features Working voltage: 4~12V; Working current: 0.8A; Motor diameter: 2.7cm; inlet opening outer diameter: 0.4c. Water flow rate: Approx. 1.2L/M (5V) Application DIY project English Manual/Spec NO Packing List 1 x Motor 1 x Hose (100cm) Dimensions: 2.56 in x 1.69 in x 1.61 in (6.5 cm x 4.3 cm x 4.1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 | (http://www.dx.com/p/236808)


(1) 229082 (http://www.dx.com/p/229082) $5.92 www.dx.com | DIY Electric Motor Mini Water Pump (http://www.dx.com/p/229082) $5.92 Brand N/A Quantity 1 Piece(s)/pack Color Silver + white Material Iron + copper + plastic Compatible Models N/A Application Testing, fish-farming, etc. Other Feature Inlet and outlet hole external diameter: 4mm; Rated voltage: 7.2V; DC voltage: 3~9V; Please note: No-load test should not take a long time; With plastic blade, Can't be inhaled impurities Packing List 1 x Pump Dimensions: 2.56 in x 1.61 in x 1.50 in (6.5 cm x 4.1 cm x 3.8 cm) Weight: 2.54 oz (72 g) | (http://www.dx.com/p/229082)


(1) 300904 (http://www.dx.com/p/300904) $8.48 www.dx.com | 5.5V- 12V Submersible Water Pump - Black (http://www.dx.com/p/300904) Voltage: 3.5-12V, head: 40-160cm. the maximum flow: 300L/H. 60 degrees below temperature resistant. - Continuous working life (24 hours non-stop work) more than 20000 hours, about 10 hours per day, water pump life for 8 years. - The inlet and outlet diameter is 8.3MM, the inner diameter 6.2MM. With 2 soft sucker, can be fixed freely. - Super mute, noise figure is 30dB Brand: N/A Quantity: 1-Piece Color: Black Material: ABS Dimensions: 1.89 in x 1.57 in x 1.06 in (4.8 cm x 4 cm x 2.7 cm) Weight: 2.52 oz (71.5 g) Packing Lis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 | (http://www.dx.com/p/300904)
(1) 185970 (http://www.dx.com/p/185970) $6.49 www.dx.com | MPX08 Micro Liquid Gear Pump w/ Silicone Tube - White (DC 5V) (http://www.dx.com/p/185970) Model MPX08 Quantity 1 Color White Material Plastic + Iron Features Start current: 2A; Perfect for DIY projects such as fish tank, model, etc. Packing List 1 x Micro pump 1 x Silicone tube (100cm) Dimensions: 2.56 in x 1.65 in x 1.54 in (6.5 cm x 4.2 cm x 3.9 cm) Weight: 3.28 oz (93 g) | (http://www.dx.com/p/185970)


(1) $6.47 | Desloo Ethernet Shield W5100 Micro-sd Card Slot for Arduino 2009 UNO Mega 1280 2560 Duemilanove http://www.amazon.com/Desloo-Ethernet-Micro-sd-Arduino-Duemilanove/dp/B00GIDHZHE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

# Failed Attempts For Reference

## Powder Dispensing

Dispensing powder proved to be quite challenging

- Large holed Granular type approach – FAILED
- Funnel container – FAILED (Didn't attempt a super-long auger approach as it was thought to fail also)
- Large bottom “Water Wheel” type approach - FAILED
- Partial Solution “Top Down” – WORKS (But needs refinement – as per actual unit)
  - Creating a scrapper that falls down as product is removed while scrapping product to a center drop hole.
  - While this worked for flour – corn starch and small holed center (1/2” pipe) will most likely still be an issue
  - Disadvantages
    - The scrapping gear must be held up while filling the cannister
    - The center shaft has large holes that leak while filling the cannister
    - A cap must be put on the end of the shaft to keep it from binding the gear
    - Filling with flour is more difficult due to motor being attached at the top
    - The flour did dispense well as shown above the can has been dispensed of flour completely without any intervention.

### **OUTDATED** Gallon Can Powder Foods Dispenser (GC-PFD-28BYJ)

The 1-Gallon powder food dispenser requires

- One Gallon Tin Can with a base diameter that measures 16.125 inches
- 28BYJ-48 5Vdc 4-Phase 5-Line Stepper Motor with ULN2003 Driver Module Board
- 3/4” Shedule 80 PVC Pipe threaded and notched the height of the tin can
- 3/4” PVC Pipe Nut (Created by cutting a PVC cap)
- 3D Printer for printing the following parts located at http://www.github.com/tgit23/ArdiChef/ → Hardware/PowderDispensers/GallonCan_ThreeQtrPipe

File-Name | Google Sketchup | Thumb | Build Instructions
MotorMountGearBox.skp | 2014 - Inches | | 1) The 28BYJ Stepper motor is bolted into this motor mount gear box (Shaft up)
MotorGear.skp | 2014 -Inches | | 2) The MotorGear is placed on the motor shaft
PipeDriverGear.skp | 2014 - Inches | | 3) The PipeDriverGear is dropped freely into the MotorMountGearBox.
Scrapper.skp | 2014 - Inches | | 4) A 3/4” Schedule 80 PVC pipe is threaded the height of the gallon can in use 5) Using a dremel with grinder stone create 2-notches vertically along the pipe for the DriverGear 6) The Scrapper is attached (glued) to the top of the 3/4” Threaded and notched PVC pipe.
GalCanBase_ThreeQtrNutBase.skp | | | 7) A PVC Nut (A cut in half PVC Cap) is glued into the CanBase 8) The CanBase is then attached to the bottom of a one-gallon tin can 9) The “MotorMountGearBox/MotorGear/PipeDriverGear” assembly is bolted to the CanBase. 10) The Threaded and Notched “PVC-Pipe/Scrapper” is threaded down the CanBase Nut till the PipeDriverGear's Notches catches the Notches in the PVC pipe.

28BYJ Stepper Motor Bolted to MotorMountGearBox.skp MotorGear.skp attached to the shaft of 28BYJ Stepper PipeDriverGear.skp placed in the MotorMountGearBox.skp | 3/4” Schedule 80 Threaded and Notched PVC Pipe Scrapper.skp glued to the top of the 3/4” PVC Pipe GalCanBase_ThreeQtrNutBase.skp with 3/4” PVC Cap nut | Thread the 3/4” Schedule 80 PVC Pipe with a 3/4” pipe threader die - the length of the height of the gallon tin can minus the height of the attaching scrapper.
Using a Dremel with a grind stone (~ 1/8” thick), notch the threaded 3/4” PVC pipe on both sides so the PipeDriverGear.skp locks rotation-ally to the pipe but freely slides vertically along the pipe. | The stepper motor drives the PipeDriverGear which turns the PVC Pipe which rotates the attached Scrapper while the Cans base with PVC nut moves (via threads) the scrapper/pipe assembly from Top-to-Bottom. | The rotating scrapper pulls the powder to the center of the PVC pipe (Drop-hole) while also pulling the scrapper a set distance down the can via the pipes threads and base nut.

### **OUTDATED** Cambells 26.25Oz Family Size Can Powder Foods Dispenser (CC-PFD-28BYJ)

The Family Size Cambells Soup Can powder food dispenser requires

- One Family Size Cambells Soup Can with a base diameter that measures 3 3/8 inches
- 28BYJ-48 5Vdc 4-Phase 5-Line Stepper Motor with ULN2003 Driver Module Board
- 1/2” Shedule 80 PVC Pipe threaded and notched the height of the tin can
- 1/2” PVC Pipe Nut (Created by cutting a PVC cap)
- 3D Printer for printing the following parts located at http://www.github.com/tgit23/ArdiChef/ → Hardware/PowderDispensers/Cambells_26.26OZ_HalfInchPipe

File-Name | Google Sketchup | Thumb | Build Instructions
MotorMountGearBox.skp | 2014 - Inches | | 1) The 28BYJ Stepper motor is bolted into this motor mount gear box (Shaft up)
MotorGear.skp | 2014 -Inches | | 2) The MotorGear is placed on the motor shaft from /PowderDispensers/GallonCan_ThreeQtrPipe
PipeDriverGear.skp | 2014 - Inches | | 3) The PipeDriverGear is dropped freely into the MotorMountGearBox.
Scrapper.skp | 2014 - Inches | | 4) A 1/2” Schedule 80 PVC pipe is threaded the height of the gallon can in use 5) Using a dremel with grinder stone create 2-notches vertically along the pipe for the DriverGear 6) The Scrapper is attached (glued) to the top of the 1/2” Threaded and notched PVC pipe.
CanBase_Campbells26.25OZ.skp | | | 7) A PVC Nut (A cut in half PVC Cap) is glued into the CanBase 8) The CanBase is then attached to the bottom of a one-gallon tin can 9) The “MotorMountGearBox/MotorGear/PipeDriverGear” assembly is bolted to the CanBase. 10) The Threaded and Notched “PVC-Pipe/Scrapper” is threaded down the CanBase Nut till the PipeDriverGear's Notches catches the Notches in the PVC pipe.

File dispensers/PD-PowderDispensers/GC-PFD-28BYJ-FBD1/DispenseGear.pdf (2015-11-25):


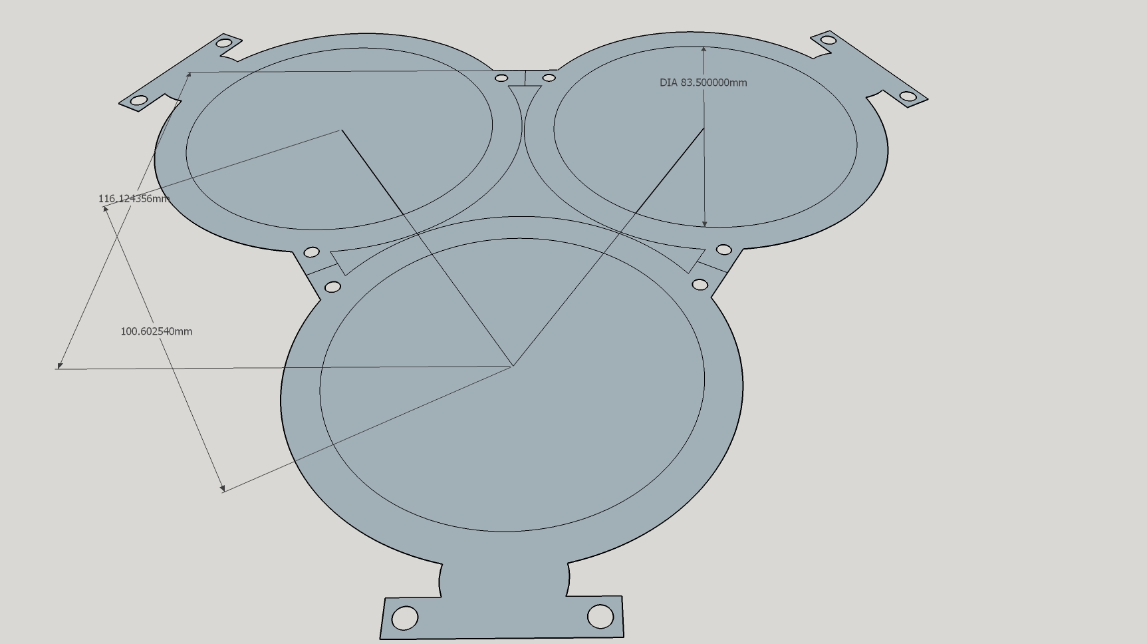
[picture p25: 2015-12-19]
ArdiChef-Model100/_images/FloorPlan.jpg

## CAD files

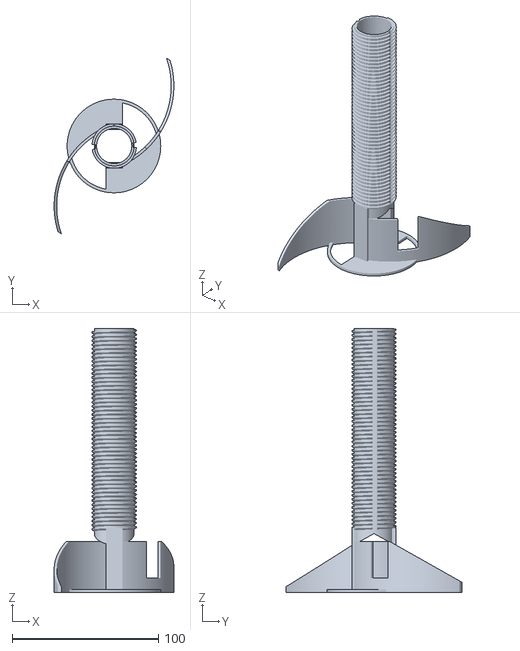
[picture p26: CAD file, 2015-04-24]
dispensers/PD-PowderDispensers/GC-PFD-28BYJ-TDS1/DispenserPipe_24D_Complete_fixed.stl
81.9 x 120.2 x 180.4

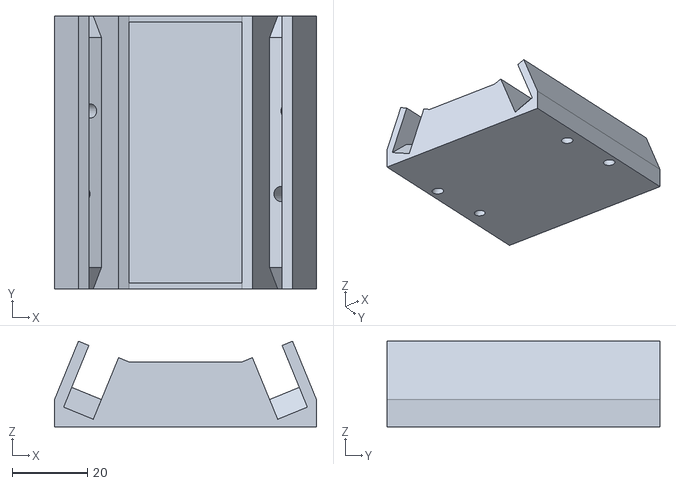
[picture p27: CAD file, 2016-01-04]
ArdiChef-Model100/StandCrossMember.stl
69.5 x 72.3 x 22.7

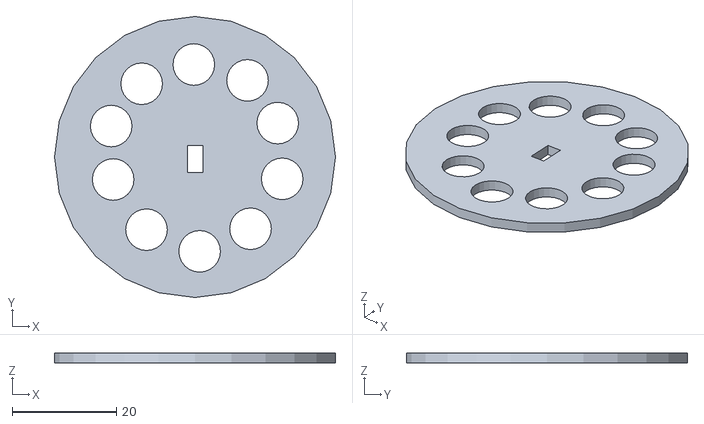
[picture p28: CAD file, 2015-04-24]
dispensers/GD-GranularDispensers/DispGear_4inHoles.stl
54.0 x 54.0 x 2.00

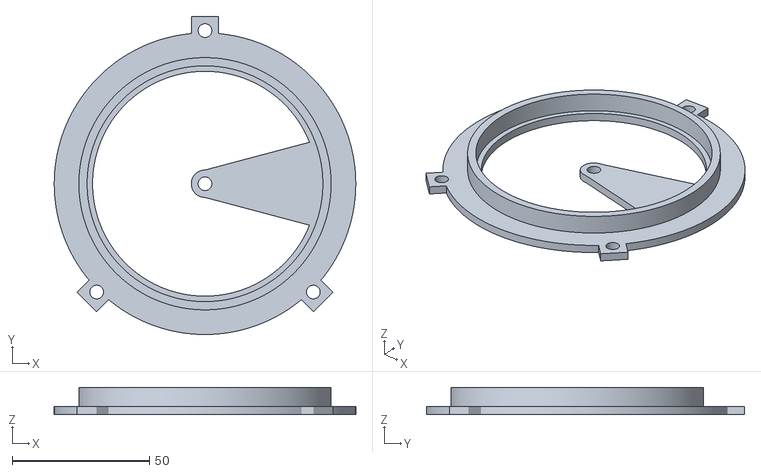
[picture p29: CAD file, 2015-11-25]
dispensers/PD-PowderDispensers/FC-PFD-28BYJ-FBD1/CanBaseBushing.stl
110.0 x 116.0 x 10.0

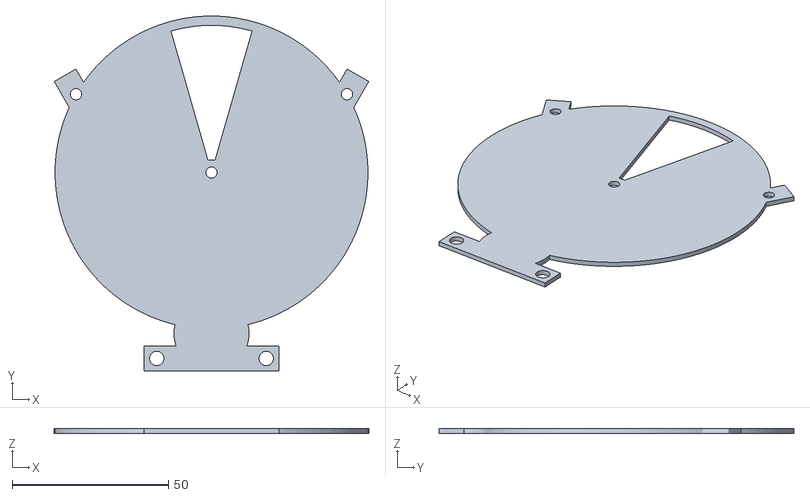
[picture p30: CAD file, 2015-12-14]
dispensers/PD-PowderDispensers/PD-FBD-28BYJ-86MM/CanisterCover.stl
100.5 x 113.5 x 1.50

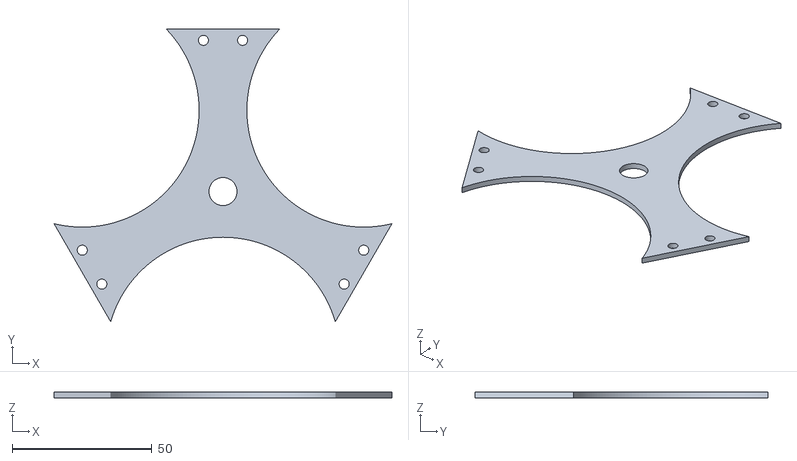
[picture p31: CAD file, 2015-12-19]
ArdiChef-Model100/CenterClamp.stl
120.8 x 104.6 x 2.00

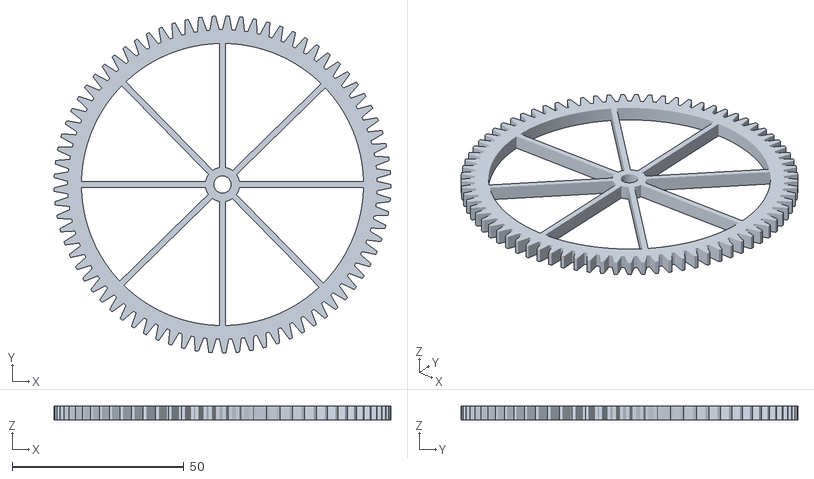
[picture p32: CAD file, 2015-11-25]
dispensers/PD-PowderDispensers/FC-PFD-28BYJ-FBD1/DispenserGear.stl
98.0 x 98.0 x 4.00

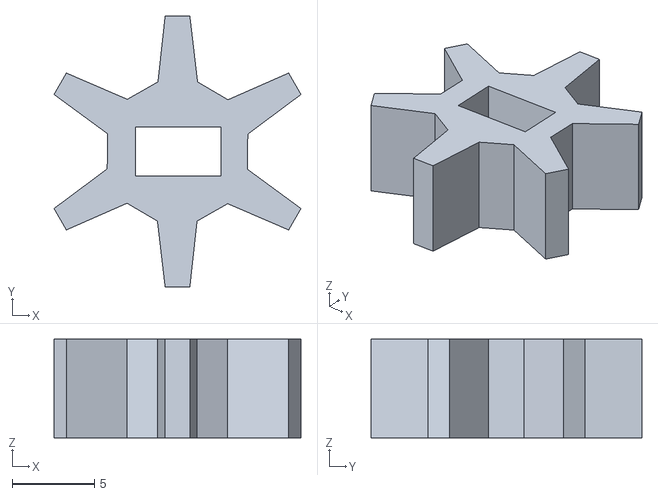
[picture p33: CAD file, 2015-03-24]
dispensers/PD-PowderDispensers/GC-PFD-28BYJ-TDS1/MotorGear.stl
15.0 x 16.5 x 6.01

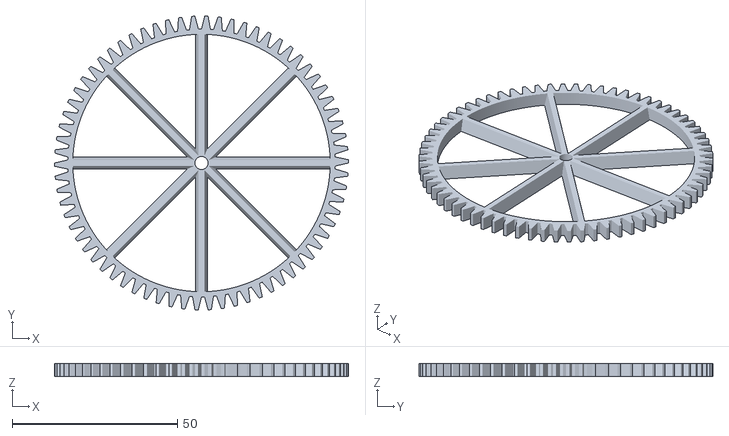
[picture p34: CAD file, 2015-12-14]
dispensers/PD-PowderDispensers/PD-FBD-28BYJ-86MM/DispenseGear.stl
89.1 x 89.1 x 4.00

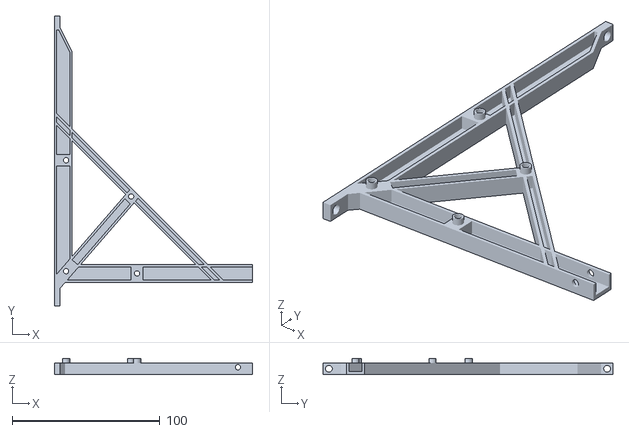
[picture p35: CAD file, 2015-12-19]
ArdiChef-Model100/StandLeg.stl
134.2 x 196.0 x 11.0

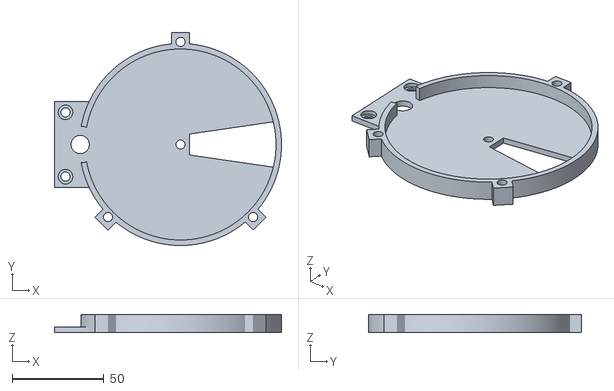
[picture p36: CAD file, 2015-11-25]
dispensers/PD-PowderDispensers/FC-PFD-28BYJ-FBD1/CanBase_28BYJ.stl
123.6 x 116.0 x 10.0

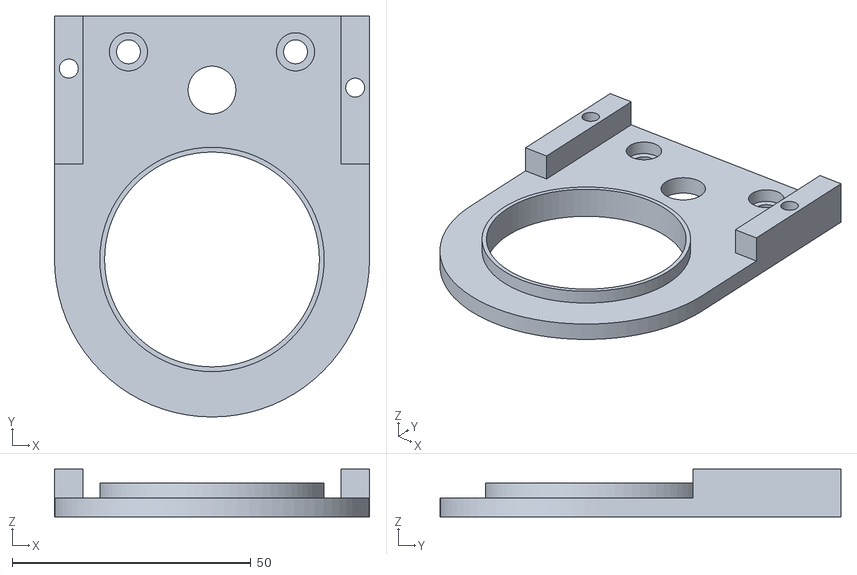
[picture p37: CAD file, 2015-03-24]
dispensers/PD-PowderDispensers/GC-PFD-28BYJ-TDS1/MotorMountGearBox_fixed.stl
66.0 x 84.0 x 10.0

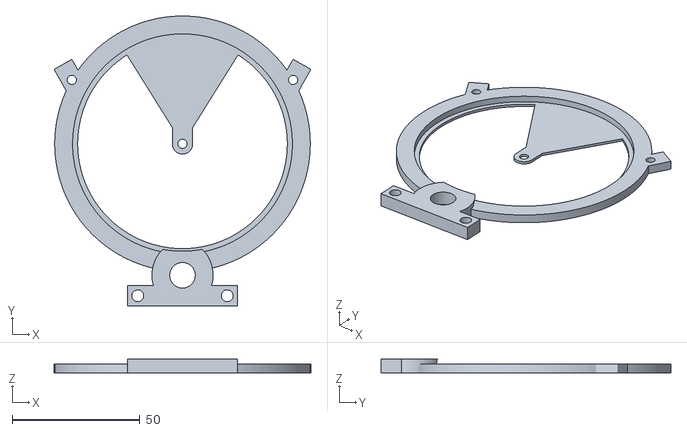
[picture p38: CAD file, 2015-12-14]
dispensers/PD-PowderDispensers/PD-FBD-28BYJ-86MM/CanisterBase-86MM.stl
100.5 x 113.5 x 5.50

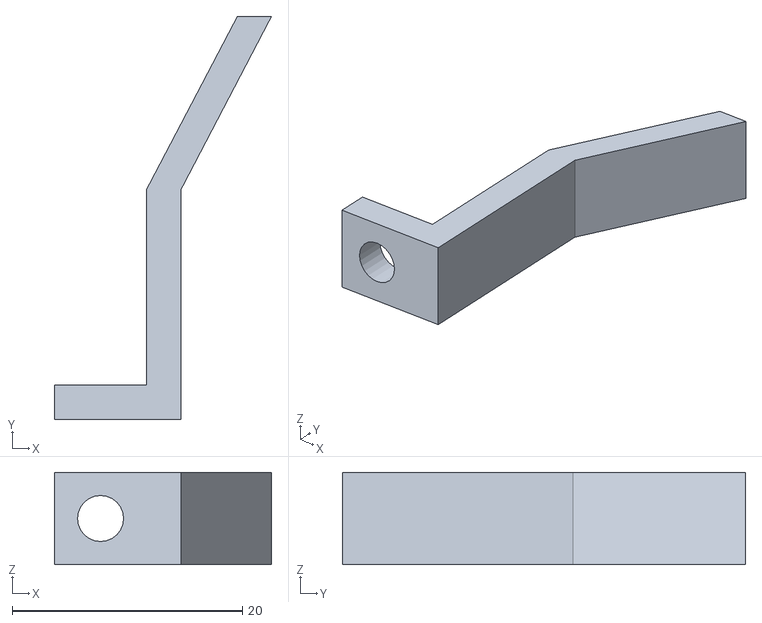
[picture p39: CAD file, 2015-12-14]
ArdiChef-Model100/Funnel-Brackets-2LiterPop.stl
18.8 x 35.0 x 8.00

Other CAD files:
dispensers/PD-PowderDispensers/GC-PFD-28BYJ-TDS1/MotorMountGearBox.stl
dispensers/PD-PowderDispensers/PD-FBD-28BYJ-86MM/MotorGear.stl
ArdiChef-Model100/Platform-For-3.stl
dispensers/PD-PowderDispensers/PD-FBD-28BYJ-86MM/CenterRing.stl
ArdiChef-Model100/SketchFiles/CenterClamp.skp
ArdiChef-Model100/SketchFiles/Funnel-Brackets-2LiterPop.skp
ArdiChef-Model100/SketchFiles/Platform-For-3.skp
ArdiChef-Model100/SketchFiles/StandCrossMember.skp
ArdiChef-Model100/SketchFiles/StandCrossMember2.skp
ArdiChef-Model100/SketchFiles/StandLeg.skp
ArdiChef-Model100/SketchFiles/StandLeg_OLD.skp
dispensers/GD-GranularDispensers/Cover.skp
dispensers/GD-GranularDispensers/DispGear_4inHoles.skp
dispensers/GD-GranularDispensers/GallonCanBase_6pt125inchBase.skp
dispensers/GD-GranularDispensers/MotorMount.skp
dispensers/GD-GranularDispensers/MotorMountSpout.skp
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

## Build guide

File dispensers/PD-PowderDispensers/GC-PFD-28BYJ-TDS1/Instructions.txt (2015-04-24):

-----------------------------------------------------------
DispenserPipe_24D_Complete.skp
-----------------------------------------------------------
The dispenser pipe is a threaded and notched pipe with
scrapper flaps used to scrape the powder from the top of
the can to the center pipe for dispensing.

Often special printer speed settings are necessary to keep
the print from falling off its base during print.

Speed Settings
Perimeters                  20 mm/s
Small Perimeters            20 mm/s
External Perimeters         70%
Infill                      40 mm/s
Solid Infill                40 mm/s
Top Solid Infill            40 mm/s
Support Material            40 mm/s
Support Material Interface  100%
Bridges                     10 mm/s
Gap fill                    10 mm/s

Travel                      40 mm/s

First Layer Speed           80%

------------
Heat            260
Bed             115

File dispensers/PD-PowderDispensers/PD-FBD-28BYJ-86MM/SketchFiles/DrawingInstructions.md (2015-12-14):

# SketchUp Model Drawing Instructions
### For Part: PD-FBD-28BYJ-85MM

-----------------------------------------------------------------------------------
## Notes
-----------------------------------------------------------------------------------
* Unless otherwise specified
    * Circles are 180-sides proportioned out on the red axis
    
* Abbreviations
    * `South` indicates the light colored axis portion - bottom of origin
    * `@` = at
    * `@+` = at intersection of ? & ?
    * `->` = to
    * `->+` = to intersect
    * `R/L` = Right and Left
    * `^` = Start at ending point of the last drawing just above
    * `#x` = Number of times (example 2x = Draw Two Times)
    * `center` = Main center of an object; associated with other drawing points
    
1. Name of Object
    - Tool @(at) Start Point
        - Length, Radius or End Point
        
-----------------------------------------------------------------------------------
## Canister Cover
-----------------------------------------------------------------------------------
1. Outer-Shell
    - Circle @ Origin
        - 50mm radius

2. Center-Fastener (#4 screw hole)
    - Circle @ origin
        - 1.8mm radius
        
3. Side-Fasteners (#4 screw hole)
    - Protractor @ origin along green axis
        - Right 4-nothes (60&deg;)
        - Left 4-notches (60&deg;)
        - *Guides will be 8-notches apart (120&deg;)*
        
    - Circles `center` @+ Guides & Outer-Shell
        - 1.8mm Radius(2x)

    - Tape @+ South Green & Outer-Shell
        - -> Center of left Side-Fastener circle center
        - -> Center of right Side-Fastener circle center
        
    - Tape @ Side-Fasteners center
        - 7mm along Tape guides(2x) outwards from Outer-Shell
        - Lines ^
            - 4mm Perpendicular R/L
            - Lines ^
                - Perpendicular ->+ Outer-Shell(2x)
    
4. Motor-Shaft-Shell
    - Calculate
        - (Dispense Gear Outer Radius) + (Motor Gear outer Radius) - (2mm mesh together)
        - (44.54545mm) + (8.909mm) - (2mm) = 51.45445mm
    - Tape @ Origin
        - 51.45mm along South green axis to mark `center`
        - Circles ^
            - 10mm Radius
            - 12mm Radius
    
5. Motor-Mount-Holes
    - Tape @ Motor-Shaft-Shell center
        - 8mm along South green axis
        - Tape ^
            - 17.5mm Perpendicular R/L to mark `center`
            - Circles ^
                - 2.3mm Radius (#6 screw hole)
                
6. Motor-Mount-Pad
    - Tape @ Motor-Mount-Hole centers(2x)
        - 4mm (Up and Right) / (Down and Left)
        - Rectangle ^
    
    *At this point delete all the guides and clean up the drawing as shown*
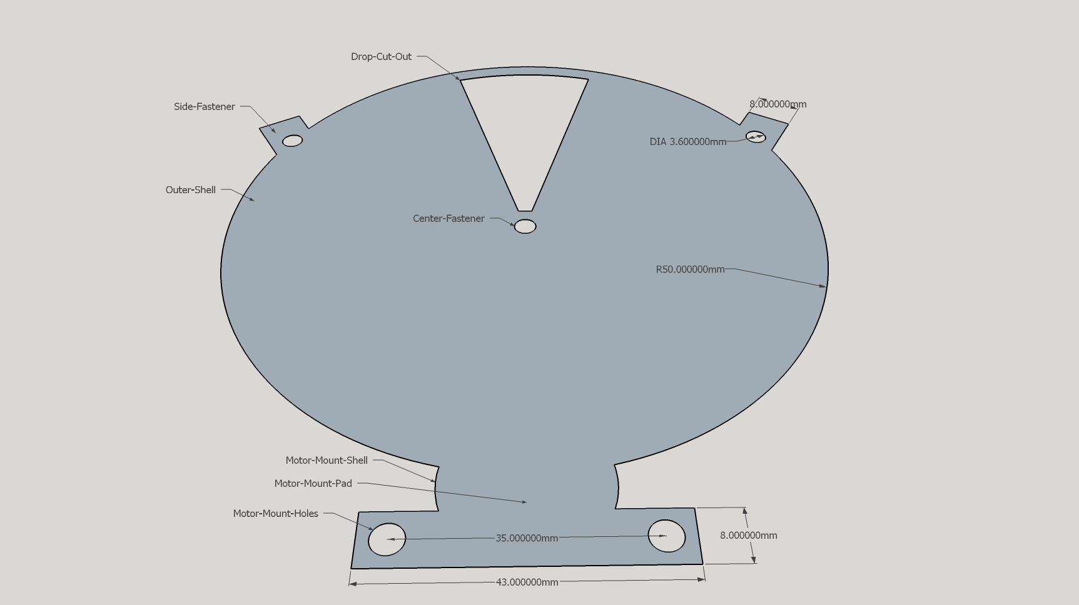
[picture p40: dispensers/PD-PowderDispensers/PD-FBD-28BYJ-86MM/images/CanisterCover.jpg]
    
    
7. Drop-Cut-Out
    - Circle @ origin
        - 47mm radius
    - Line @ origin
        - -> 8 circle sides R/L of Green axis
        - *end-point to end-point (opening) should be 25.9mm*
    - Tape @ origin
        - 4mm along green axis
        - Line ^
            - Perpendicular R/L ->+ Drop-Cut-Out lines
    *Clean up the drawing *
    
8. Finish
    - Push @ Canister Cover Model
        - 1.5mm Tall

-----------------------------------------------------------------------
#CENTER RING
-----------------------------------------------------------------------
1. Outer-Shell
    - Circle @ origin
        - 50mm radius
        
2. Inner-Shell
    - Circle @ origin
        - 47mm radius
        
3. Side-Fasteners (preform Canister Cover Step #3)
4. Motor-Mount (preform Canister Cover Steps #4,5,6)

    *At this point delete all the guides and clean up the drawing as shown leaving 3mm outer edges*
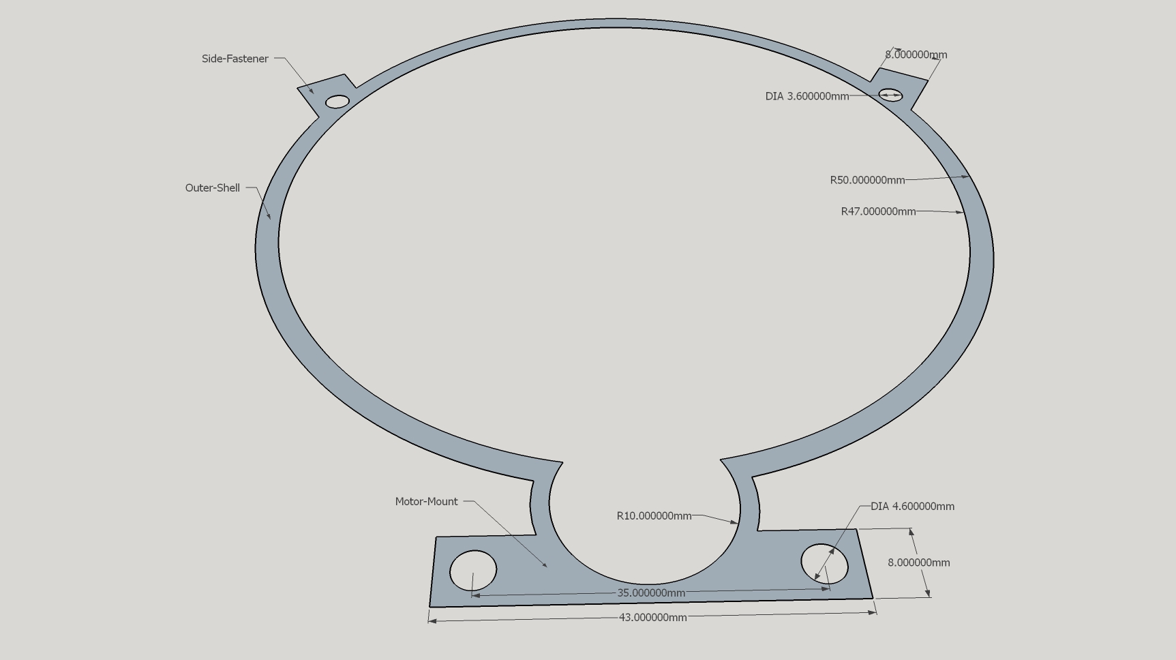
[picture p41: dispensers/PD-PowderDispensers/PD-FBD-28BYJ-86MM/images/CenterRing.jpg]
    

8. Finish
    - Push @ Center Ring Model
        - 6mm Tall

-----------------------------------------------------------------------
#CANISTER BASE (83MM)
-----------------------------------------------------------------------
1. Outer-Shell
    - Circle @ origin
        - 50mm radius
        - 43mm radius

2. Can-Seat
    - Circle @ origin
        - 41mm radius
        
3. Side-Fasteners (preform Canister Cover Step #3)
4. Motor-Mount (preform Canister Cover Steps #4,5,6)
    - Circle @ Motor-Shaft-Shell center
        - 5mm radius

5. Drop-Cover-Flap
    - Protractor @ origin
        - 32&deg; L/R of green axis
        - Lines @ origin
            - ->+ Inner-Shell along protractor guides
    - Circle @ origin
        - 1.8mm radius
        - 4mm radius
        - Lines @+ Red Axis & ^
            - ->+ Protractor Lines

    *At this point delete all the guides and clean up the drawing as shown*
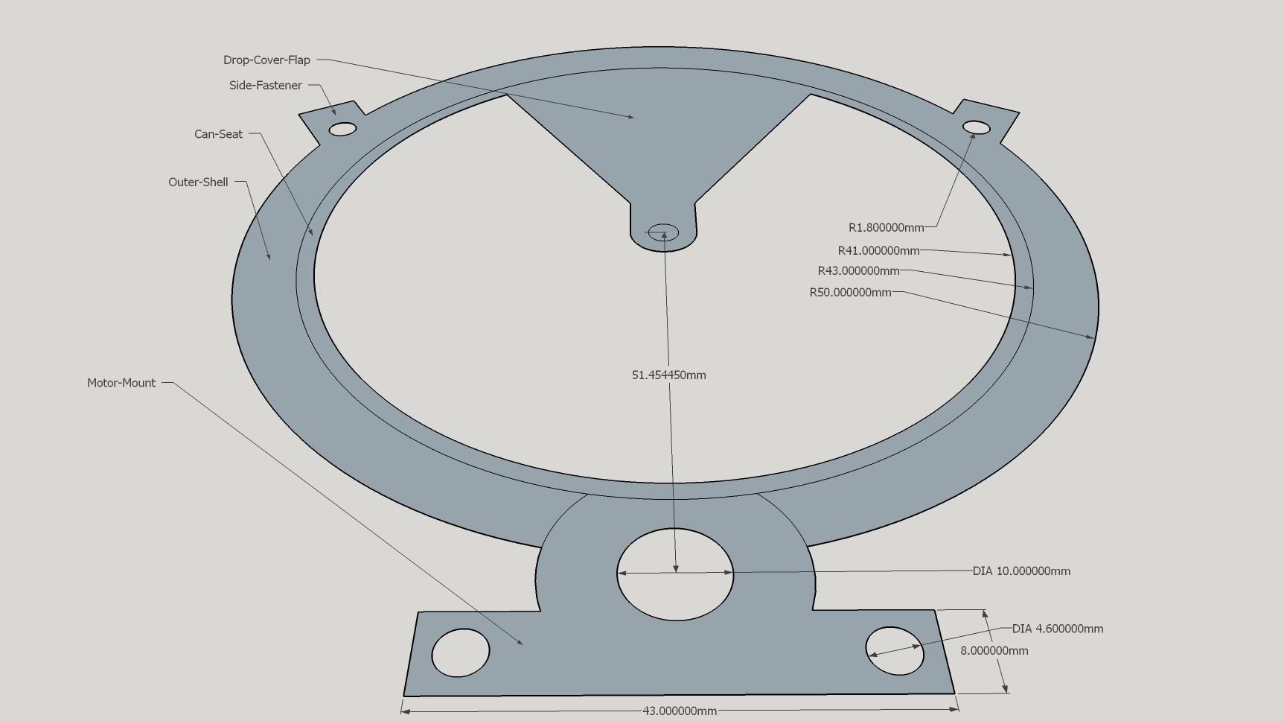
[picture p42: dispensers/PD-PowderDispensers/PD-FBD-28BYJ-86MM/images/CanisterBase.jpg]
    

6. Finish
    - Push @ Motor-Mount
        - 5.5mm Tall
        - Move @ Circle Section +Outer-Shells inner circle & Motor-Mount
            - 1mm Towards origin (*Supply a lip over the Can-Seat to hold canister*)
    - Push @ Outer-Shell
        - 3.5mm Tall
    - Push @ Can-Seat
        - 1mm Tall

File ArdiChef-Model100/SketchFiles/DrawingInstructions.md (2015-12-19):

# SketchUp Model Drawing Instructions
### For Part: ArdiChef Model-100

-----------------------------------------------------------------------------------
## Notes
-----------------------------------------------------------------------------------
* Unless otherwise specified
    * Circles are 180-sides proportioned out on the red axis
    
* Abbreviations
    * `South` indicates the light colored axis portion - bottom of origin
    * `@` = at
    * `@+` = at intersection of ? & ?
    * `->` = to
    * `->+` = to intersect
    * `R/L` = Right and Left
    * `^` = Start at ending point of the last drawing just above
    * `#x` = Number of times (example 2x = Draw Two Times)
    * `center` = Main center of an object; associated with other drawing points
    
1. Name of Object
    - Tool @(at) Start Point
        - Length, Radius or End Point
        
-----------------------------------------------------------------------------------
## Center Clamp
-----------------------------------------------------------------------------------
1. Three Can Positioning
    - Protractor @ origin along red axis
        - 60&deg; towards green axis
        - 120&deg;
    - Line @ origin along protractor guides
        - 100.6mm length
    - Circle @ ^
        - 41.75mm Radius

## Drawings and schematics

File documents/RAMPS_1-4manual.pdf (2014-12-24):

# RAMPS 1.4 http://reprap.org/wiki/ramps

This is open hardware: you can redistribute it and/or modify it under the terms of the GNU General Public License as published by the Free Software Foundation, either version 3 of the License, or (at your option) any later version.

This hardware design is distributed in the hope that it will be useful, but WITHOUT ANY WARRANTY; without even the implied warranty of MERCHANTABILITY or FITNESS FOR A PARTICULAR PURPOSE. See the GNU General Public License for more details.

You should have received a copy of the GNU General Public License along with this program. If not, see <http://www.gnu.org/licenses/>.

!!! Reversing input power, and/or inserting stepper drivers incorrectly will destroy electronics and cause fire hazard!!!

Test all electronics thoroughly before placing into service.

Do not leave power supplied to electronics unattended, or run machines unattended due to the risk of fire and malfunction.

This is NOT a toy and it contains
small and sharp parts. Children can
choke or suffocate by swallowing small objects. Keep all parts away from children and never leave printer/parts unattended.

Bill of Materials
Qty Part Name | Value | Package
3 C1,C5,C8 | 10uF | 153CLV-0405
1 C2 | 100nF | C0805
6 C3,C4,C6,C7,C9,C10 | 100uF | 153CLV-0605
2 D1,D2 | 1N4004 | DO41-10
1 F1 | MFR500 | MFR500
1 F2 | MFR1100 | MFR1100
1 LED1 | green | CHIP-LED0805
3 LED2,LED3,LED4 | red | CHIP-LED0805
3 Q1,Q2,Q3 | STP55NF06L TO220BV
5 R1,R7,R11,R21,R22 | 4.7K (1%) | R0805
8 R2,R3,R4,R5,R6,R8,R9,R10100k | R0805
1 R12 | 1K | R0805
3 R23,R24,R26 | 1.8K | R0806
3 R13,R14,R15 | 10r | R0805
5 R16,R17,R18,R19,R20 | 10k | R0805
1 S1 | B3F-3100 | B3F-31XX
1 U$2 | 282837-6 | 282837-6
1 X4 | MSTBA4 | MSTBA4
1 | 0.1” 18x2 pin
8 | 0.1” 2x3 pin
5 | 0.1” 8x1 pin
2 | 0.1” 6x1 pin
6 | 0.1” 4x1 pin
2 | 0.1” 24x1 female
4 | 0.1” 8x1 female
15 | 0.1” 2 pin jumper

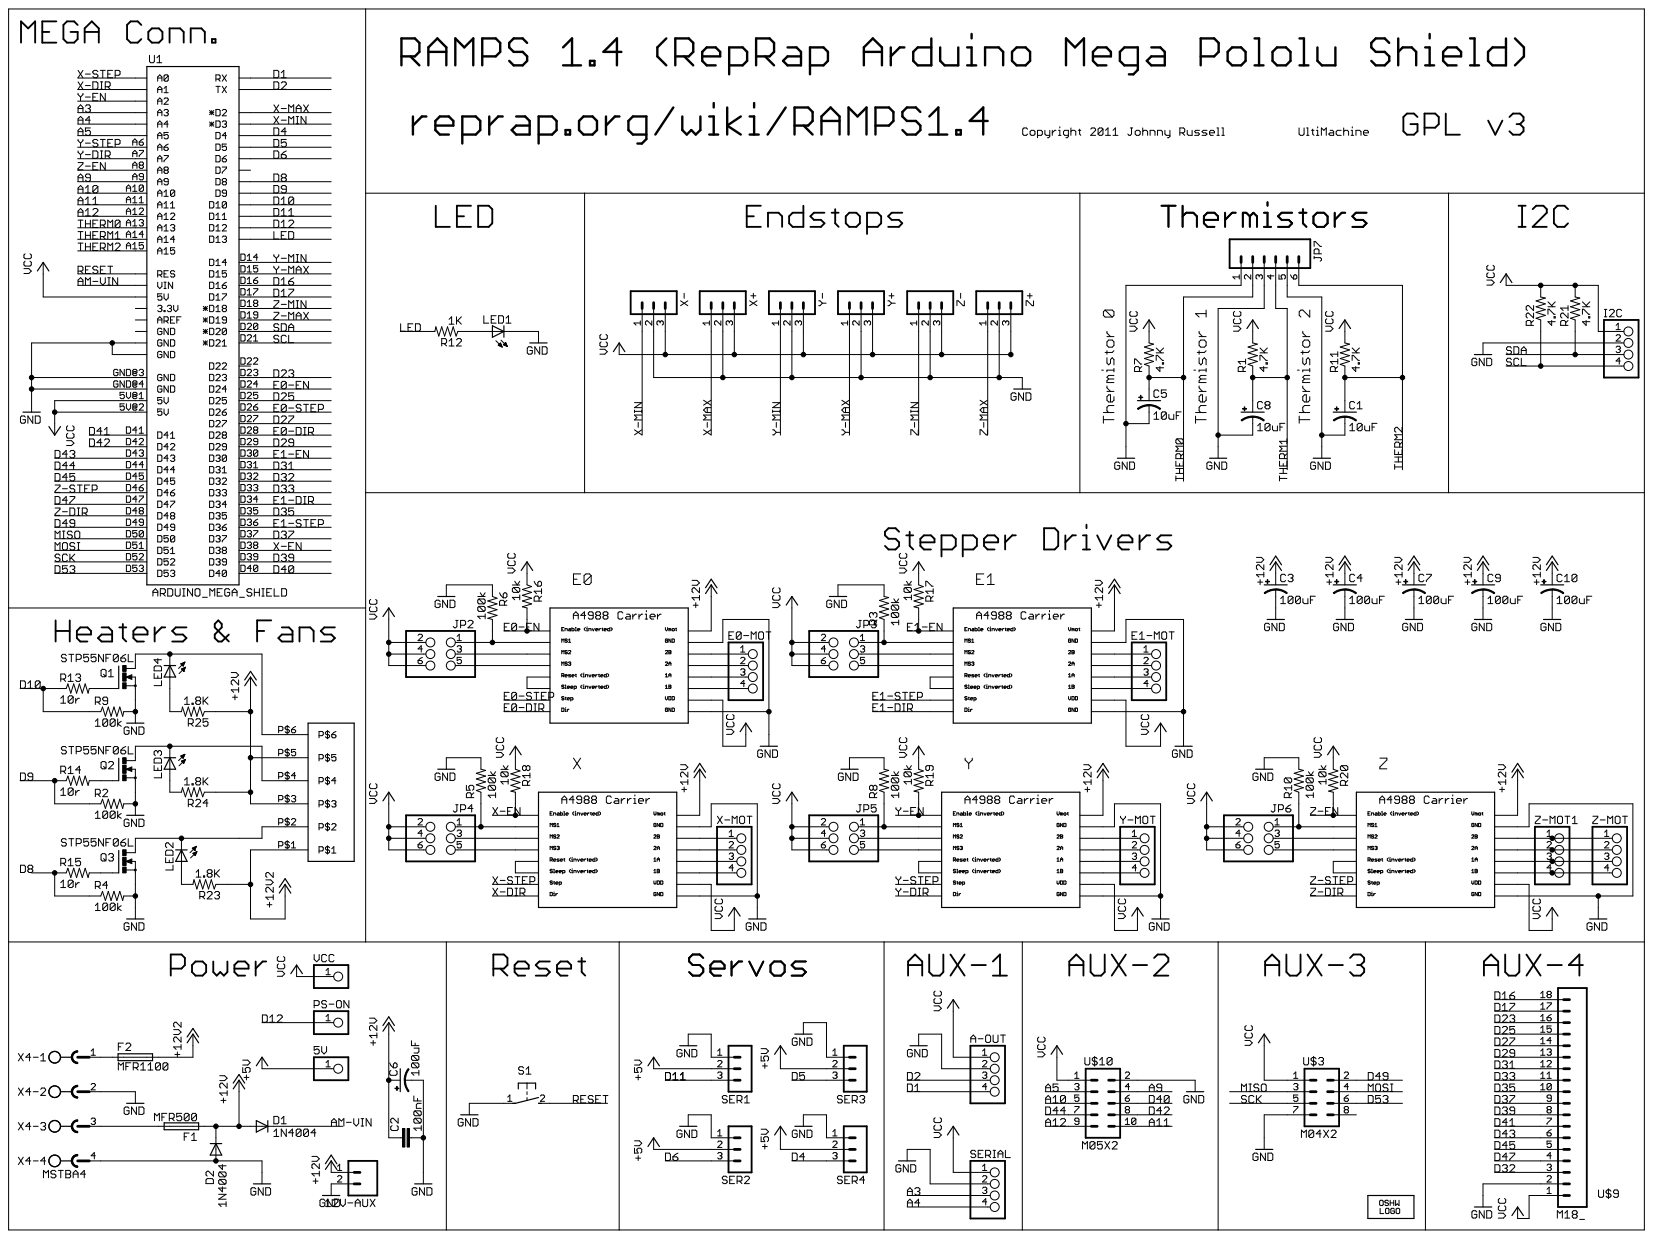
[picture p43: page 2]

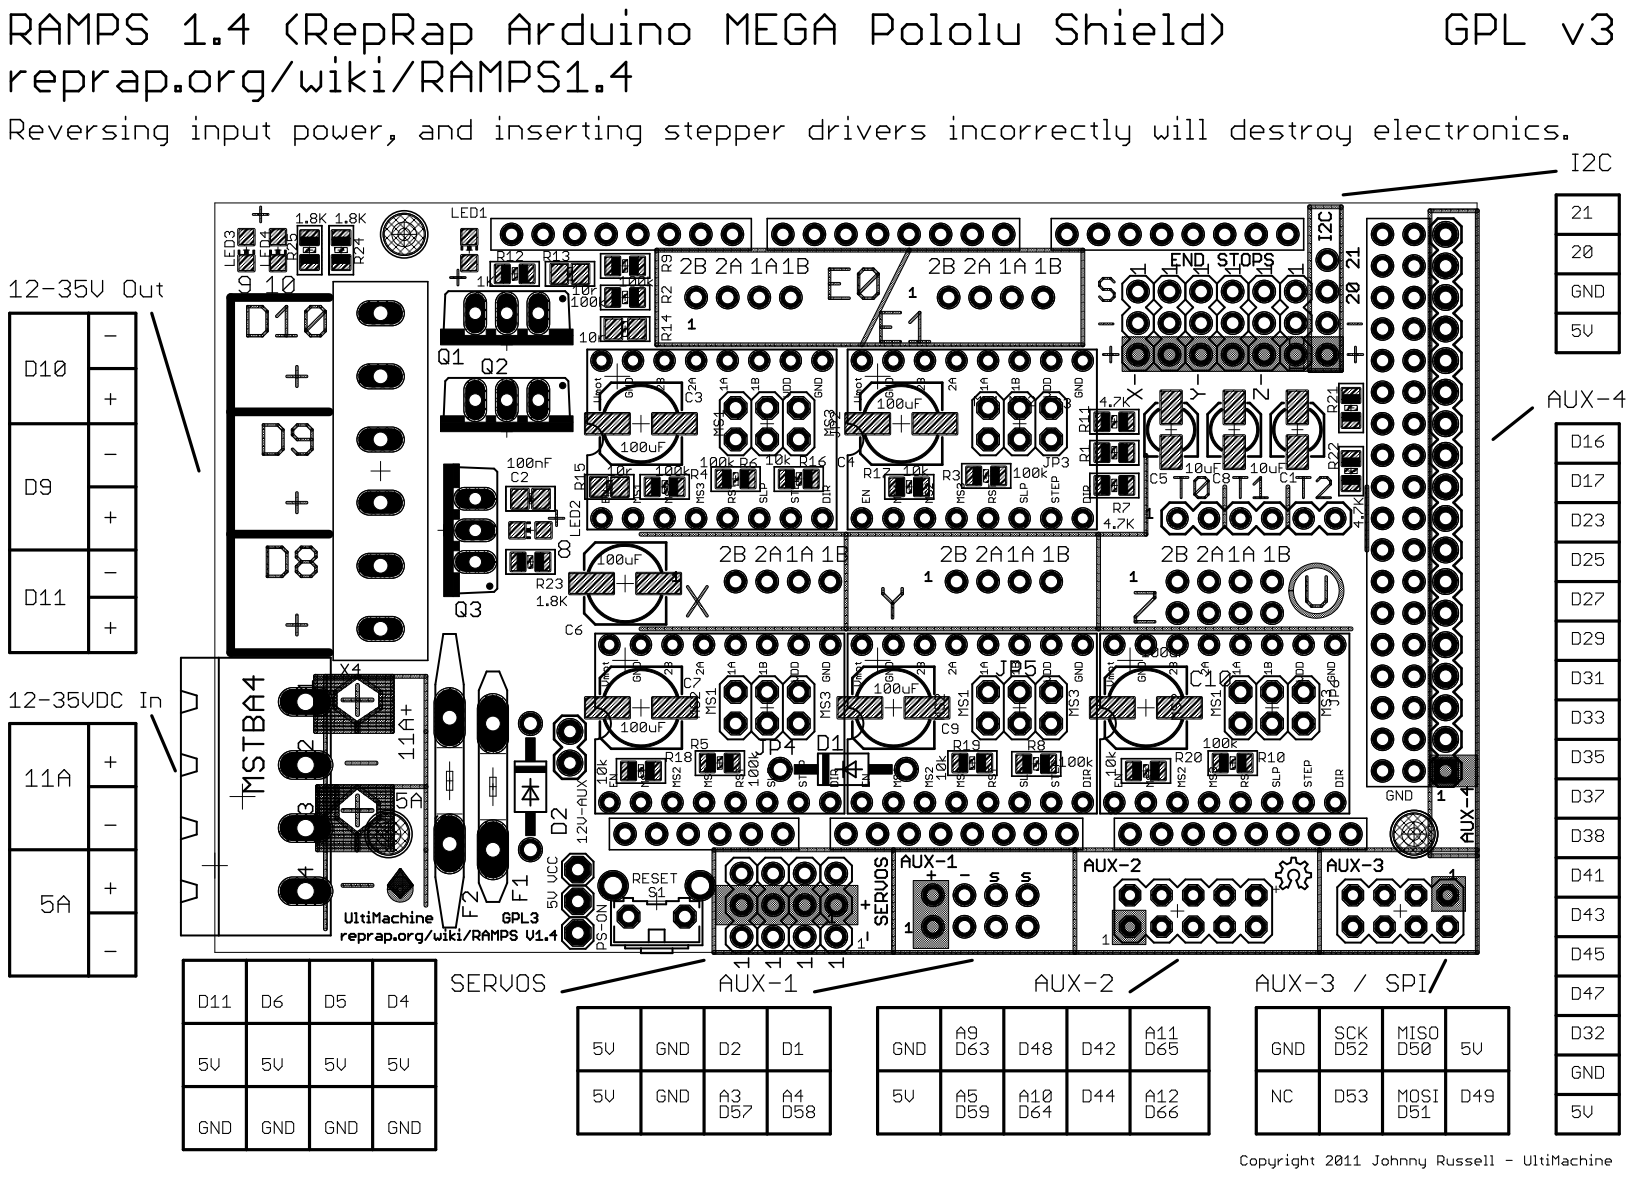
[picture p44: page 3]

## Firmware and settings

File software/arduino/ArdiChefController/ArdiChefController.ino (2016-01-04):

/************************************************************************//**
 * @file ArdiChefController.ino
 * @brief  ArdiChef's 'Main' Sketch used for all Arduino board(s).
 *    Primary Functions:
 *    @li Web Server - |Optionally| host EWS through ethernet shield
 *    @li I2C Communications - Recieve, Parse, and Execute I2C Commands
 *    @li Manage Ports - Load JSON, Start/Stop Motors, Cancel in Motion
 * @details
 *    Arduino Mega2560
 *    Desloo Ethernet Shield w/5100 Wiznet
 *    (3) ULN2003 Step Motor Driver boards
 * @authors
 *    tgit23      11/2015       Original code.
 * @notes
 * 
 *    File Dependancies:
 *      A4988Driver(.cpp,.h)
 *      DriverBase(.cpp,.h)
 *      PortsCollection(.cpp,.h)
 *      Settings.h
 *      ULN2003Driver(.cpp,.h)
 *      WebServerSTPlus(.cpp,.h)
 *      
 *    Library Dependancies:
 *      Ethernet
 *      SD
 *      SPI
 *      ArduinoJson
 *      Wire
 * @todo
 * @see http://www.ArdiChef.com
 ******************************************************************************/
#include "Settings.h"

#if IS_WEBSERVER>0
  #include "WebServerSTPlus.h"        // Include WebServer Code
  #include <Ethernet.h>               // Include Ethernet Shield Library
  #include <utility/w5100.h>          // Include w5100 library
  #include <utility/socket.h>         // Include socket library
  #include <SD.h>                     // Include SD-Card library
  #include <SPI.h>                    // Include SPI library for SD-Card
  #include <ArduinoJson.h>            // Include a JSON parser for SD-Card files
  WebServerSTPlus *webserver;         // Initialize 'webserver' pointer
#endif


#define SERIAL_BUFFER_SIZE 64         // Largest I2C or Serial recievable text
#if SLAVE_I2C_ADDR>0                  // Include the Wire.h library for I2C communications
  #include <Wire.h>
#endif

#include "PortsCollection.h"          // Include I/O Ports code
PortsCollection Ports;                // Initialize the 'Ports' Object

char postreq[48] = {0};
bool once = false;                    // Used to trigger a one-time command in the loop()
/***************************************************************************************
 * setup()
 * @param void
 * @return void
 **************************************************************************************/
void setup() {
  #if DEBUG>0                               // Begin Serial Monitor for DEBUG Messages
    Serial.begin(SERIAL_BAUD);
  #endif
  #if SLAVE_I2C_ADDR==0                     // Setup Ports using JSON File if "Master" Arduino
    Ports.SetupWithSDFile(SD_SETUP_FILE);
  #else
    Wire.begin();                           // Activate I2C Communications if "Slave" Arduino
  #endif
  
  #if IS_WEBSERVER>0                        // Setup Arduino Web-Host Settings
    byte mac[] = { MAC };                   // See Settings.h
    IPAddress ip( IP_ADDRESS );
    IPAddress gateway( GATEWAY );
    IPAddress subnet( SUBNET );
    #if USE_DHCP>0
      webserver = new WebServerSTPlus(mac,ip,gateway,subnet,true,80);
    #else
      webserver = new WebServerSTPlus(mac,ip,gateway,subnet,false,80);
    #endif
  #endif
} 

/***************************************************************************************
 * loop()
 * @param void
 * @return void
 **************************************************************************************/
void loop() {

  #if IS_WEBSERVER>0                      // Call the 'webserver' doloop()
    for (int c=0;c<48;c++) postreq[c] = '\0';
    webserver->doloop(postreq);
    if ( strlen(postreq) > 0 ) { Ports.Command(postreq); }
    myStuff();
  #endif
  Ports.doloop();                         // Call the 'Ports' doloop()
  
  if ( !once ) { 
    once = true;
    Ports.Command("2,30000,0;");
    Ports.Command("1,30000,0;");
    Ports.Command("0,30000,0;");
  }
}

void myStuff() {
  if(Serial.available()) { if(Serial.read() == 'r') webserver->ShowSockStatus(); }
  webserver->checkSockStatus();
}

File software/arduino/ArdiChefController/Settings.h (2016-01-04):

/************************************************************************//**
 * @file Settings.h
 * @brief File for ArdiChef configuration settings
 * @details
 * @authors
 *    tgit23      11/2015       Original Author
 * @todo
 * @see http://www.ArdiChef.com
 ******************************************************************************/
#ifndef SETTINGS_H
#define SETTINGS_H

#include <Arduino.h>
/** @brief Activates the Arduino WebServer code to host the EWS through
 *  an attached ethernet shield */
#define IS_WEBSERVER 1
/** @brief Set to '0' if the Arduino is the "Master" Arduino board;  Otherwise
 *  assign an I2C decimal address for the "Slave" Arduino Board. */
#define SLAVE_I2C_ADDR 0
/** @brief Set to '1' to show debug messages in the 'Serial Monitor' */

#define USE_DHCP 0
#define IP_ADDRESS 192,168,0,25
#define GATEWAY 192,168,0,1
#define SUBNET 255,255,255,0
#define MAC 0xDE,0xAD,0xBE,0xEF,0xFE,0xEC

#define DEBUG 1
#define SD_SETUP_FILE "/JSON/INGRED~1.JSO"
#define SERIAL_BAUD 250000
#define SD_CSPIN 4
#define W5100_CSPIN 10


/******************************************************************************/
// Setup - No custom settings below this line
#if DEBUG>0
    #define DB1L(x) Serial.println x
    #define DB1(x) Serial.print x
#else
  #define DB1L(x)
  #define DB1(x)
#endif
#if DEBUG>1
  #define DB2L(x) Serial.println x
  #define DB2(x) Serial.print x
#else
  #define DB2L(x)
  #define DB2(x)
#endif
  
#endif

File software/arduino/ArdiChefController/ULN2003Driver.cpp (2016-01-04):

#include "ULN2003Driver.h"

/******************************************************************************************
 * @brief Initializer / Constructor
 * @param Pin1 - Arduino output digital pin number connected to 1st step motor wire
 * @param Pin2 - Arduino output digital pin number connected to 2nd step motor wire
 * @param Pin3 - Arduino output digital pin number connected to 3rd step motor wire
 * @param Pin4 - Arduino output digital pin number connected to 4th step motor wire
 * @param PulseWidth - Set the Step Pulse Width time (smaller=faster)
 *****************************************************************************************/
ULN2003Driver::ULN2003Driver(int Pin1, int Pin2, int Pin3, int Pin4, unsigned long PulseWidth) {
  DB1(("ULN2003Driver::Constructor( Pin1="));DB1((Pin1));
  DB1((",Pin2="));DB1((Pin2));
  DB1((",Pin3="));DB1((Pin3));
  DB1((",Pin4="));DB1((Pin4));
  DB1((",PulseWidth="));DB1((PulseWidth));DB1L((" )"));
  
  mPin1 = Pin1; pinMode(mPin1, OUTPUT); digitalWrite(mPin1, LOW);
  mPin2 = Pin2; pinMode(mPin2, OUTPUT); digitalWrite(mPin2, LOW);
  mPin3 = Pin3; pinMode(mPin3, OUTPUT); digitalWrite(mPin3, LOW);
  mPin4 = Pin4; pinMode(mPin4, OUTPUT); digitalWrite(mPin4, LOW);
  mPulseWidth = PulseWidth;
  return;
}

/******************************************************************************************
 * @brief Command(ULN2003-Command)
 *    The ULN2003Driver 'Commands' are in the form "<port>,<steps>,<dir>;"
 * @param[in] Command - The text command to process
 * @return void
 *****************************************************************************************/
void ULN2003Driver::Command(const char* DCommand) {
  DB1(("ULN2003Driver::Command( '"));DB1((DCommand));DB1((F("' ) -> ")));
  
  char pinsBuff[32]; int port = -1;
  sscanf(DCommand, "%d,%lu,%d;", &port, &msteps, &mdir);
  
  // Display parsing
  DB1((F("Port=")));DB1((port));
  DB1((F(",Steps=")));DB1((msteps));
  DB1((F(",Dir=")));DB1L((mdir));
  
  return;
}

/******************************************************************************************
 * @brief doloop() Keep active routine.  Processes text commands asynchronously
 * @return void
 *****************************************************************************************/
void ULN2003Driver::doloop() {

  if ( msteps < 1 ) return;                   // If no steps need action then exit
  
  unsigned long t = micros();                 // Record time
  if ( (t - mlast_uSec) > mPulseWidth ) {     // If time passed > PulseWidth
    mlast_uSec = t; msteps--;                 // Mark time; Preform a step
    DB2(("ULN2003Driver::doloop() -> "));
    DB2(("Steps:"));DB2((msteps));
    DB2((", uSecPast:"));DB2L((t - mlast_uSec));
    digitalWrite(mPin1, MotorSteps[mSubStep][0]); 
    digitalWrite(mPin2, MotorSteps[mSubStep][1]);
    digitalWrite(mPin3, MotorSteps[mSubStep][2]);
    digitalWrite(mPin4, MotorSteps[mSubStep][3]);
    if(mdir>0) mSubStep++; else mSubStep--;
    if(mSubStep>7) mSubStep=0;
    if(mSubStep<0) mSubStep=7;
    
    if (msteps < 1 ) {                        // Shut-off pins on last step
      digitalWrite(mPin1, LOW);
      digitalWrite(mPin2, LOW);
      digitalWrite(mPin3, LOW);
      digitalWrite(mPin4, LOW);
    }
  }

  return;
}

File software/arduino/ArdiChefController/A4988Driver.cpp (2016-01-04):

/************************************************************************//**
 * @file A4988Driver.cpp
 * @brief  Port Driver for the Allegro A4988 Stepper Motor Driver.
 * @code
 *    exmaple code
 * @endcode
 * @authors 
 *    tgit23        11/2013       Original
 ******************************************************************************/
#include "A4988Driver.h"

/***********************************************************************************//**
 * @brief A4988Driver() Initializer
 *    Drivers are initialized by the 'PortsCollection' object.
 * @param[in] stepPin - Arduino digital pin number connected to the A4988 'step' pin
 * @param[in] dirPin - Arduino digital pin number connected to the A4988 'dir' pin
 * @param[in] PulseWidth - Essentially the speed; low=fast, high=slow
 * 
 * <B>Example:</B>@code{.cpp}
 *    A4988Driver *driver;
 *  driver = new A4988Driver(6,7,1000); @endcode
 **************************************************************************************/
A4988Driver::A4988Driver(int stepPin, int dirPin, unsigned long PulseWidth) {
  DB1(("A4988Driver::Constructor( stepPin = "));DB1((stepPin));DB1((" , dirPin = "));DB1((dirPin));
  DB1((" , PulseWidth = "));DB1((PulseWidth));DB1L((" )"));
  
  mstepPin = stepPin;
  mdirPin = dirPin;
  mPulseWidth = PulseWidth;
  pinMode(stepPin, OUTPUT);
  pinMode(dirPin, OUTPUT);
  return;
}

/***********************************************************************************//**
 * @brief Command("port,steps,dir;") - Execute an A4988Driver command.
 * @param[in] DCommand - The Driver Command text to be executed
 *
 * <B>Example:</B>@code{.cpp}
 *    Port.Command("0,30000,1;"); @endcode
 **************************************************************************************/
void A4988Driver::Command(const char* DCommand) {
  DB1((F("A4988Driver::Command( '")));DB1((DCommand));DB1((F("' ) -> ")));
  
  int port = 0; //char pinsBuff[32]
  sscanf(DCommand, "%31d %31lu %31d", port, &msteps, &mdir);
  if ( mdir>0 ) {
    digitalWrite(mdirPin, LOW);
  } else {
    digitalWrite(mdirPin, HIGH);
  }
  
  // Display parsing
  DB1((F("Steps=")));DB1((msteps));DB1((F(", Dir=")));DB1L((mdir));
  return;
}

/***********************************************************************************//**
 * @brief doloop()
 *    Trigger function - needs to be called inside the main sketch loop()
 **************************************************************************************/
void A4988Driver::doloop() {
  
  
  if ( msteps < 1 ) return;
  unsigned long t = micros();
  if ( (t - mlast_uSec) > mPulseWidth ) {
    mlast_uSec = t; msteps--;
    DB2((F("A4988Driver::doloop() -> ")));
    DB2((F("PulsePin:")));DB2((mstepPin));
    DB2((F(", Steps:")));DB2((msteps));
    DB2((F(", uSecPast:")));DB2L((t - mlast_uSec));
    if ( digitalRead(mstepPin) == HIGH ) {
      digitalWrite(mstepPin, LOW);
    } else {
      digitalWrite(mstepPin, HIGH);
    }
  }
  return;
}

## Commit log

2014-12-24 Updated document and folders (Initial)
    [CanBase_Campbells26.25OZ.skp, CanBase_Campbells26.25OZ.stl, CanBase_Campbells26.25OZ_MEAS.skp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]
2014-12-25 Added Simple 28BYJ Motor Drive software / Updated doc.
2014-12-31 Doc update and printed 3D pipe
2014-12-31 Printed pipe and bi-directional software added
    [4Threads.skp, CanBase.skp, FullThread.skp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]
2015-02-20 Started Funnel Auger approach to dispensing powders
    [CanBase.skp, CanBase.stl, FunnelAugerMotorMountEnd.skp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]
2015-03-24 Fine Thread printed pipe added. Flour dispensing is good.
    [4Threads.skp, CanBase.skp, CanBase.stl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]
2015-04-24 New powder dispenser with printed pipe
    [CanBase_1Thread.skp, CanBase_24D_1Thread.skp, CanBase_2Thread.skp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]
2015-11-25 Added FC-PFD-28BYJ-FBD1 powder dispenser and Arduino Server code.
    [CanBaseBushing.skp, CanBaseBushing.stl, CanBase_24D_1Thread.skp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]
2015-12-07 Updates to EWS, ArdiChefController - need I2C Ingredient ratio transformation and message passing.
2015-12-14 Starting Initial Release
    [CanBaseBushing.skp, CanBaseBushing.stl, CanBase_24D_1Thread.skp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]
2016-01-04 Recipe edit implemented; doxygen files added
    [StandCrossMember.skp, StandCrossMember.stl, StandCrossMember2.skp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]
